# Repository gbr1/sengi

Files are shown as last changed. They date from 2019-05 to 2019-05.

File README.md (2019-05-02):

# sengi
This repository contains designs for Sengi carrier board.<br>
This board is designed as "developer board" for Erwhi Hedgehog.
<br>
sengi_photo
<br>
board

Other repos:
- [sengi firmware](https://github.com/gbr1/sengi-firmware)
- [sengi ROS node](https://github.com/gbr1/sengi_ros)

<br>
<br>

***Copyright (c) 2019 Giovanni di Dio Bruno under MIT license.***

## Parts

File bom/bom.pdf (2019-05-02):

### component list

description | ID | pkg | part | qty
22uF | C1 | 0805 | GRT21BR61E226ME13L | 1
4.7uF | C2 | 0603 | CGB3B1X5R1A475K055AC | 1
100uF | C3, C4 | 0805 | GRM21BR60J107ME15L | 2
220nF | C5 | 0603 | GCM188R71E224KA55D | 1
100nF | C6, C8, C11, C12, C14, C16, C19, C20, C21, C23, C24, C25, C26, C27, C28, C31, C32 | 0402 | CL05F104ZO5NNNC | 17
1uF | C7 | 0603 | CL10A105KQ8NNNC | 1
470nF | C9 | 0402 | GRT155C81C474ME01D | 1
100uF | C10, C17, C22 | 0603 | F980J107MMAAXE | 3
10uF | C18 | EIA3216 | TAJA106K006RNJ | 1
10nF | C29 | 0402 | C0402C103K4RECAUTO | 1
2.2uF | C30 | 0402 | GRT155C81C225KE13D | 1
BNO055 | IC1 | LGA 28 | BNO055 | 1
NB679A | IC2 | QFN-12 2x3 | NB679AGD-P | 1
STM32F103C8T6 | IC3 | LQFP48 | STM32F103C8T6 | 1
DRV8833PWP | IC4 | TSSOP16 | DRV8833PWP | 1
1.5uH | L1 | 6x6 | NRS6028T1R5NMGJ | 1
LED BLUE | LED1, LED2, LED3 | 0603 | LTST-C193TBKT-5A | 3
LED RED | LED4 | 0603 | LTST-C190KRKT | 1
BAS40-05-7-F | Q2 | SOT23 | BAS40-05-7-F | 1
10k | R1, R6, R13, R18 | 0402 | RR0510P-103-D | 4
100k | R2, R19, R20 | 0402 | RR0510P-104-D | 3
1k | R3, R17 | 0402 | RR0510P-102-D | 2
2M | R4 | 0603 | RC0402JR-072ML | 1
3.3 | R5 | 0603 | RL0816S-3R3-F | 1
270k | R10 | 0402 | RC0402FR-07270KL | 1
150k | R11 | 0402 | CPF0402B150KE1 | 1
4k7 | R12 | 0402 | RC0402FR-074K7L | 1
22 | R14, R15 | 0402 | RC0402FR-0722RL | 2
1k5 | R16 | 0402 | RC0402FR-071K5L | 1
100 | R21 | 0402 | RR0510P-101-D | 1
MCP2221A | U1 | QFN 4x4 | MCP2221A-I/ML | 1
AZ1117IH-3.3 | U2 | SOT23 | AZ1117IH-3.3TRG1 | 1
BM02B-SRSS-TB | X1, X2 | | BM02B-SRSS-TB | 2
BM04B-SRSS-TB | X4, X5 | | BM04B-SRSS-TB | 2
BM10B-SRSS-TB | X3 | | BM10B-SRSS-TB | 1
B2P-VH(LF)(SN) | XA1, XA2 | | B2P-VH(LF)(SN) | 2
8MHz | Y1 | | 8MHz - CSTNE8M00GH5L000R0 | 1

1

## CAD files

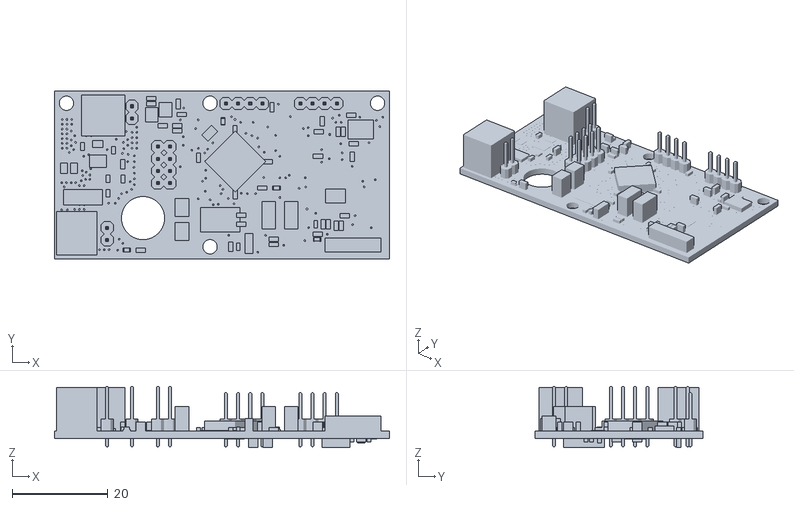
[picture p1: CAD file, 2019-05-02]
3d/carrier_sengi_personal v2.stl
70.0 x 35.0 x 12.8

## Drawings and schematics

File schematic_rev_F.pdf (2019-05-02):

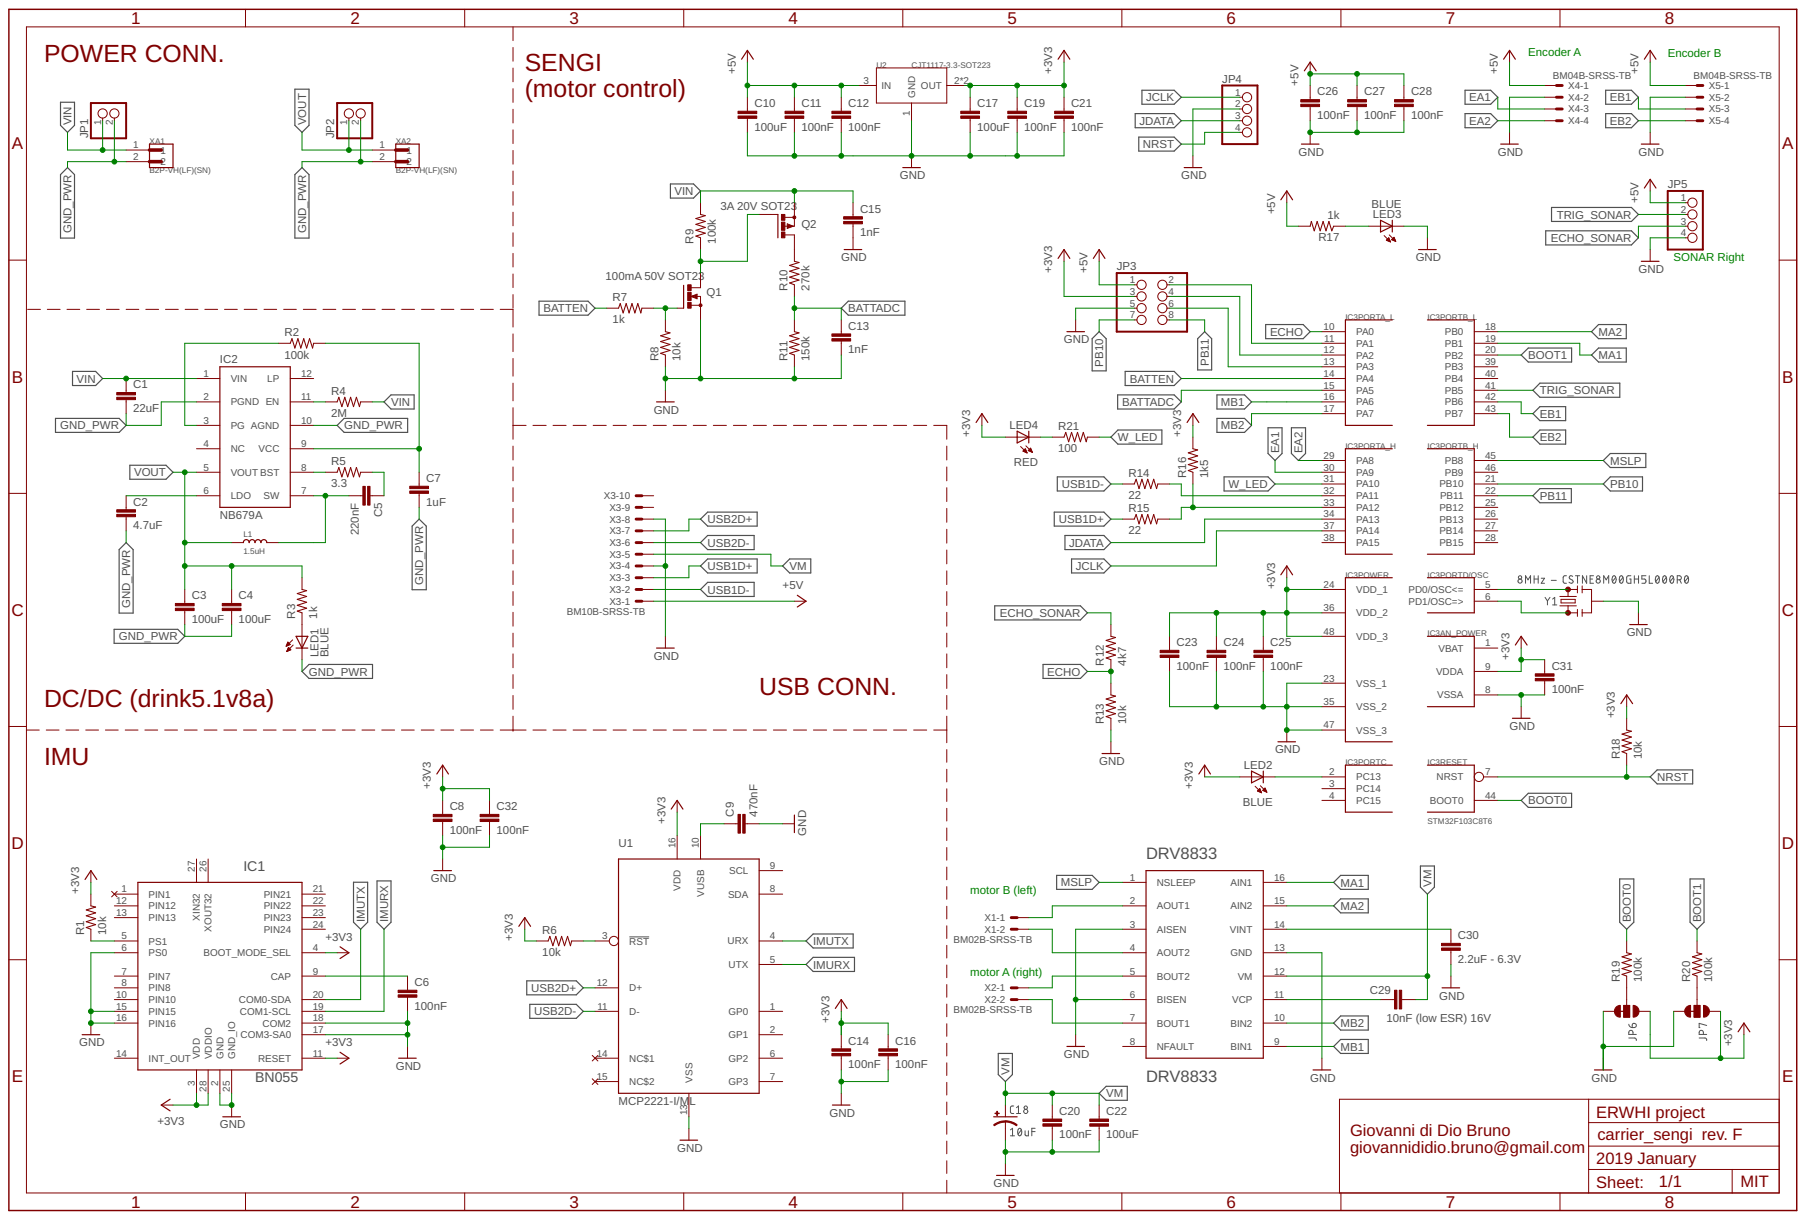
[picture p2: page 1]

ECHO_SONAR | 4

3 4
5 6
7 8

Giovanni di Dio Bruno
giovannididio.bruno@gmail.com

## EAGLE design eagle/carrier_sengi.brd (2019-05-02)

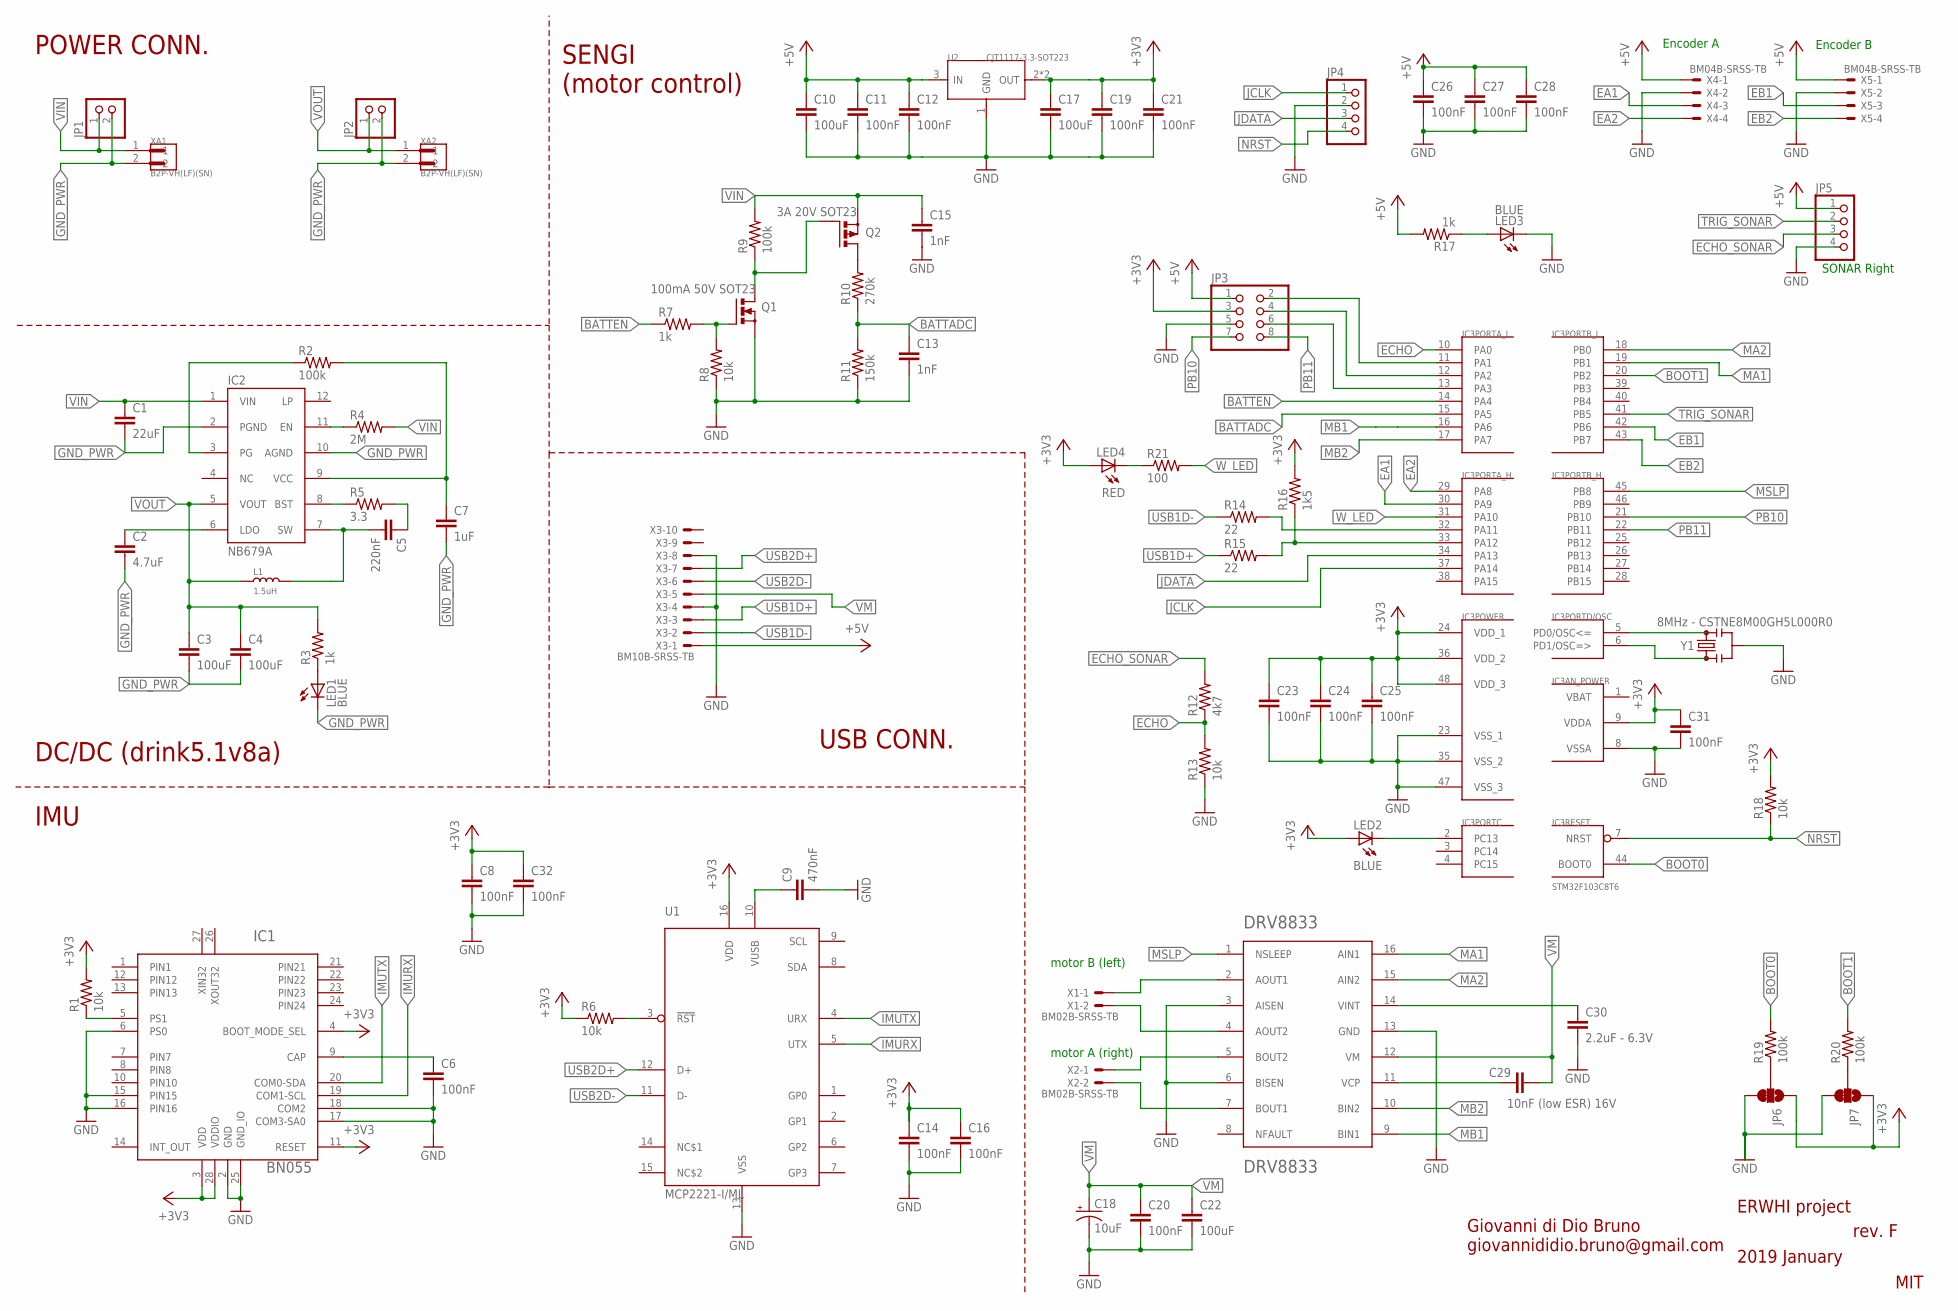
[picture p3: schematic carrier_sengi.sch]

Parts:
C1: 22uF; C0805
C2: 4.7uF; C0603
C3, C4: 100uF; C0805
C5: 220nF; C0603
C6, C8, C11, C12, C14, C16, C19, C20, C21, C23, C24, C25, C26, C27, C28, C31, C32: 100nF; C0402
C7: 1uF; C0603
C9: 470nF; C0402
C10, C17, C22: 100uF; C0603
C13, C15: 1nF; C0402
C18: 10uF; EIA3216
C29: 10nF (low ESR) 16V; C0402
C30: 2.2uF - 6.3V; C0402
IC1: BN055; LGA-28_3.80X5.20/0.5
IC2: NB679A; QFN12_2X3
IC3: STM32F103C8T6; TQFP48
IC4: DRV8833PWP; SOP65P640X120-17N
JP1, JP2: PINHD-1X2; 1X02
JP3: PINHD-2X4; 2X04
JP4, JP5: PINHD-1X4; 1X04
JP6, JP7: JUMPER-SMT_3_1-NC_TRACE_NO-SILK; SMT-JUMPER_3_1-NC_TRACE_NO-SILK
L1: 1.5uH; SMD-2P-L6.0XW6.0XH3.0MM
LED1, LED2, LED3: BLUE; CHIP-LED0603
LED4: RED; CHIP-LED0603
Q1: 100mA 50V SOT23; SOT-23
Q2: 3A 20V SOT23; SOT-23
R1, R6, R8, R13, R18: 10k; R0402
R2, R9, R19, R20: 100k; R0402
R3, R7, R17: 1k; R0402
R4: 2M; R0603
R5: 3.3; R0603
R10: 270k; R0402
R11: 150k; R0402
R12: 4k7; R0402
R14, R15: 22; R0402
R16: 1k5; R0402
R21: 100; R0402
U1: MCP2221-I/ML; QFN16-4X4
U2: CJT1117-3.3-SOT223; SOT-223
X1, X2: BM02B-SRSS-TB
X3: BM10B-SRSS-TB
X4, X5: BM04B-SRSS-TB
XA1, XA2: B2P-VH(LF)(SN); JST_B2P-VH(LF)(SN)
Y1: 8MHz - CSTNE8M00GH5L000R0; RESONATOR-SMD-3.2X1.3

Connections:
+3V3: C8.1, C14.1, C16.1, C17.1, C19.1, C21.1, C23.1, C24.1, C25.1, C31.1, C32.1, IC1.3 (VDD), IC1.4 (BOOT_MODE_SEL), IC1.11 (RESET), IC1.28 (VDDIO), IC3.9 (VDDA), IC3.24 (VDD_1), IC3.36 (VDD_2), IC3.48 (VDD_3), JP3.3, JP6.1, JP7.1, LED2.A, LED4.A, R1.2, R6.1, R16.2, R18.2, U1.16 (VDD), U2.2 (OUT), U2.TER (OUT)
+5V: C10.1, C11.1, C12.1, C26.1, C27.1, C28.1, JP3.1, JP5.1, R17.2, U2.3 (IN), X3.1, X4.1, X5.1
BATTADC: C13.1, IC3.15 (PA5), R10.1, R11.2
BATTEN: IC3.14 (PA4), R7.1
BOOT0: IC3.44 (BOOT0), R19.2
BOOT1: IC3.20 (PB2), R20.2
EA1: IC3.30 (PA9), X4.3
EA2: IC3.29 (PA8), X4.4
EB1: IC3.42 (PB6), X5.3
EB2: IC3.43 (PB7), X5.4
ECHO: IC3.10 (PA0), R12.1, R13.2
ECHO_SONAR: JP5.3, R12.2
GND: C6.2, C8.2, C9.2, C10.2, C11.2, C12.2, C13.2, C14.2, C15.2, C16.2, C17.2, C18.-, C19.2, C20.2, C21.2, C22.2, C23.2, C24.2, C25.2, C26.2, C27.2, C28.2, C30.2, C31.2, C32.2, IC1.2 (GND), IC1.6 (PS0), IC1.15 (PIN15), IC1.16 (PIN16), IC1.17 (COM3-SA0), IC1.18 (COM2), IC1.25 (GND_IO), IC3.8 (VSSA), IC3.23 (VSS_1), IC3.35 (VSS_2), IC3.47 (VSS_3), IC4.3 (AISEN), IC4.6 (BISEN), IC4.13 (GND), JP3.5, JP4.2, JP5.4, JP6.3, JP7.3, LED3.C, Q1.P2 (S), R8.1, R11.1, R13.1, U1.13 (VSS), U2.1 (GND), X3.4, X3.8, X4.2, X5.2, Y1.2
GND_PWR: C1.2, C2.2, C3.2, C4.2, C7.2, IC2.2 (PGND), IC2.10 (AGND), JP1.2, JP2.2, LED1.C, XA1.2, XA2.2
IMURX: IC1.19 (COM1-SCL), U1.5 (UTX)
IMUTX: IC1.20 (COM0-SDA), U1.4 (URX)
JCLK: IC3.37 (PA14), JP4.1
JDATA: IC3.34 (PA13), JP4.3
MA1: IC3.19 (PB1), IC4.16 (AIN1)
MA2: IC3.18 (PB0), IC4.15 (AIN2)
MB1: IC3.16 (PA6), IC4.9 (BIN1)
MB2: IC3.17 (PA7), IC4.10 (BIN2)
MSLP: IC3.45 (PB8), IC4.1 (NSLEEP)
unnamed: IC3.5 (PD0/OSC<=), Y1.3
unnamed: IC3.6 (PD1/OSC=>), Y1.1
unnamed: JP6.2, R19.1
unnamed: LED4.C, R21.1
unnamed: IC3.32 (PA11), R14.2
unnamed: IC3.33 (PA12), R15.2, R16.1
unnamed: JP7.2, R20.1
unnamed: IC3.2 (PC13), LED2.C
unnamed: IC4.2 (AOUT1), X1.1
unnamed: IC4.4 (AOUT2), X1.2
unnamed: IC4.5 (BOUT2), X2.1
unnamed: IC4.7 (BOUT1), X2.2
unnamed: C30.1, IC4.14 (VINT)
unnamed: C29.2, IC4.11 (VCP)
unnamed: LED3.A, R17.1
unnamed: IC3.11 (PA1), JP3.2
unnamed: IC3.12 (PA2), JP3.4
unnamed: IC3.13 (PA3), JP3.6
unnamed: C6.1, IC1.9 (CAP)
unnamed: IC1.5 (PS1), R1.1
unnamed: C9.1, U1.10 (VUSB)
unnamed: R6.2, U1.3 (!RST)
unnamed: IC2.11 (EN), R4.1
unnamed: IC2.3 (PG), R2.1
unnamed: C2.1, IC2.6 (LDO)
unnamed: IC2.8 (BST), R5.1
unnamed: C5.1, R5.2
unnamed: C5.2, IC2.7 (SW), L1.2
unnamed: C7.1, IC2.9 (VCC), R2.2
unnamed: LED1.A, R3.1
unnamed: Q1.P1 (G), R7.2, R8.2
unnamed: Q2.P3 (D), R10.2
unnamed: Q1.P3 (D), Q2.P1 (G), R9.1
NRST: IC3.7 (NRST), JP4.4, R18.1
PB10: IC3.21 (PB10), JP3.7
PB11: IC3.22 (PB11), JP3.8
TRIG_SONAR: IC3.41 (PB5), JP5.2
USB1D+: R15.1, X3.3
USB1D-: R14.1, X3.2
USB2D+: U1.12 (D+), X3.7
USB2D-: U1.11 (D-), X3.6
VBAT: IC3.1 (VBAT)
VIN: C1.1, C15.1, IC2.1 (VIN), JP1.1, Q2.P2 (S), R4.2, R9.2, XA1.1
VM: C18.+, C20.1, C22.1, C29.1, IC4.12 (VM), X3.5
VOUT: C3.1, C4.1, IC2.5 (VOUT), JP2.1, L1.1, R3.2, XA2.1
W_LED: IC3.31 (PA10), R21.2

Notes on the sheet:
Encoder A
Encoder B
SONAR Right
motor A (right)
motor B (left)
Giovanni di Dio Bruno giovannididio.bruno@gmail.com
MIT
2019 January
ERWHI project
IMU
DC/DC (drink5.1v8a)
POWER CONN.
USB CONN.
SENGI (motor control)
rev. F

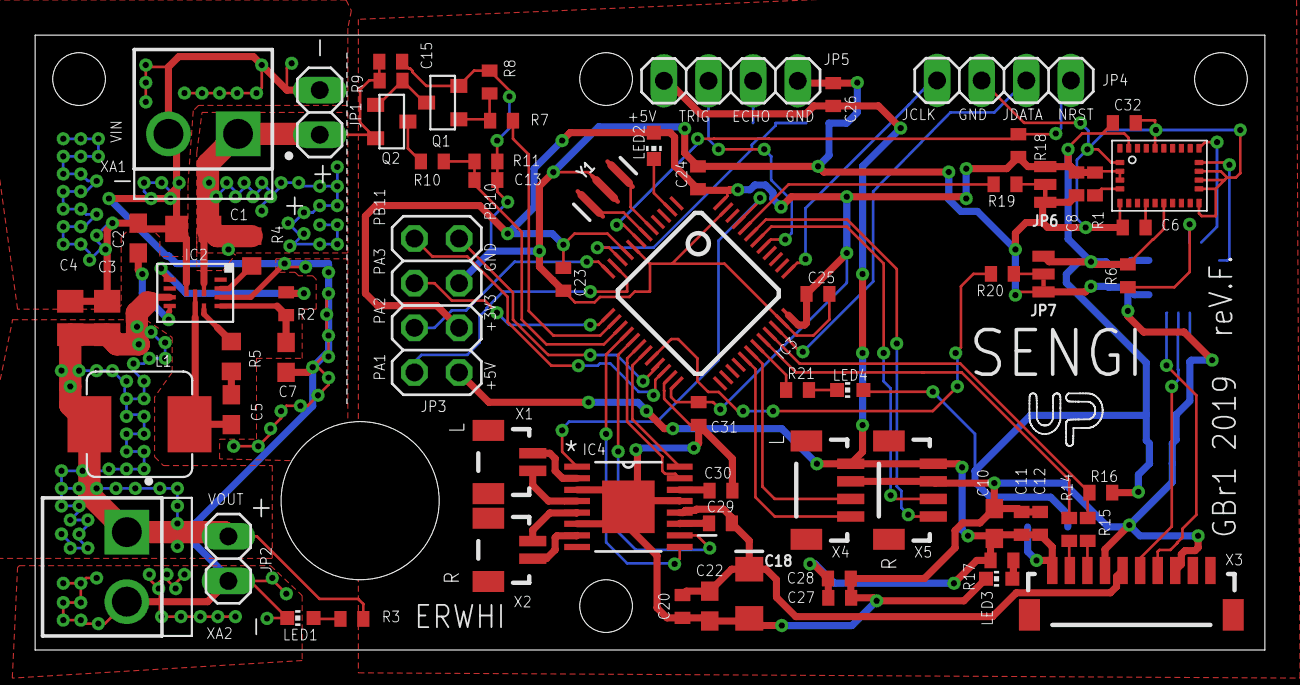
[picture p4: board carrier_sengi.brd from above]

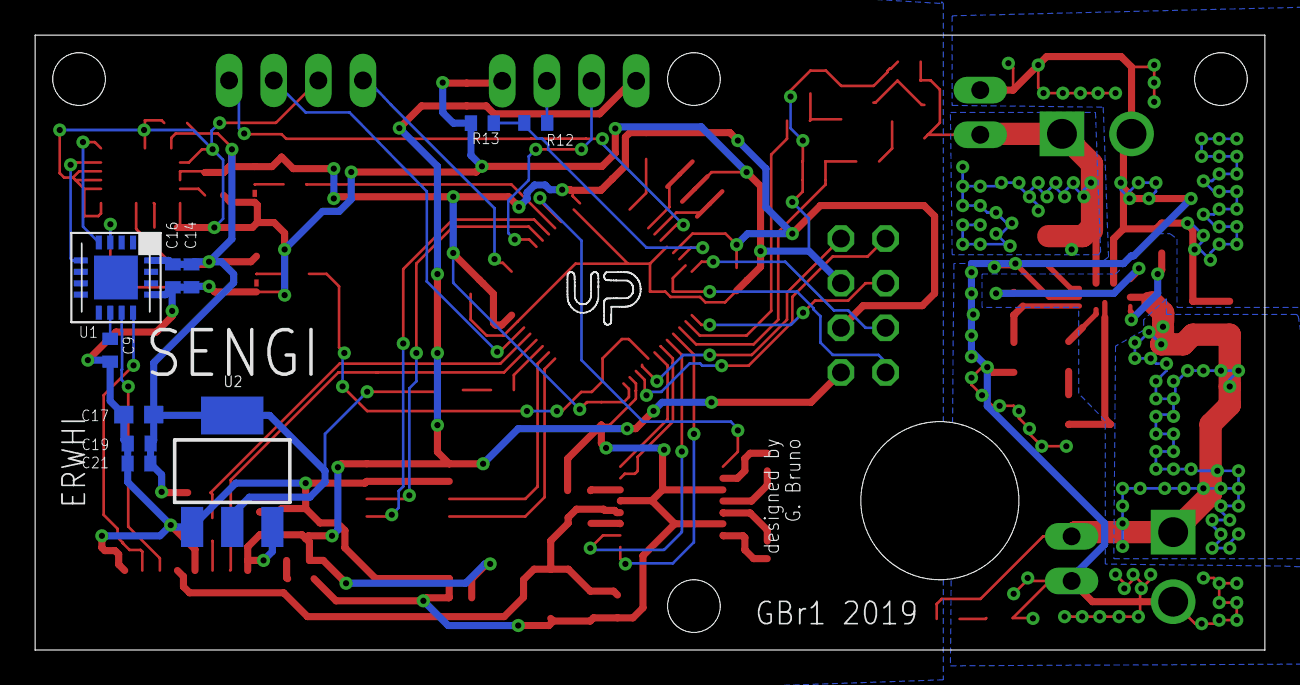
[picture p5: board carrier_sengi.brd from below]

Board: 2 copper layers, 70.0 x 35.0 mm, 83 parts (11 on the bottom side), 68 nets.

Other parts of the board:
U$1, U$2: LOGO_UP

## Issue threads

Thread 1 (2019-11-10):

PCB

schmidtp1, 2019-11-10:
@gbr1, where can I get the PCB? Can you recommend any place to order?

gbr1, 2019-11-10:
I often use  [ALL PCB](https://www.allpcb.com/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).

I think that for cheap PCBs are all the same about quality, so check also [PCBway](https://www.pcbway.com/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) and [JCLPCB](https://jlcpcb.com/)

Closed 2019-11-10.

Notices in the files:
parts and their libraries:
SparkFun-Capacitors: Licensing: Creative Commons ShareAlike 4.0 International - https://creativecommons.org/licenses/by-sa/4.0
